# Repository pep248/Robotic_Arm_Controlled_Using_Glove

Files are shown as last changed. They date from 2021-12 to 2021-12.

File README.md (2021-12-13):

# Robotic arm controlled using an electronic glove

This repository contains a project with the mechanical design of a robotic arm meant to copy the movements of a user.
The arm has been mechanically designed using SolidWorks, and has been programed using Arduino.

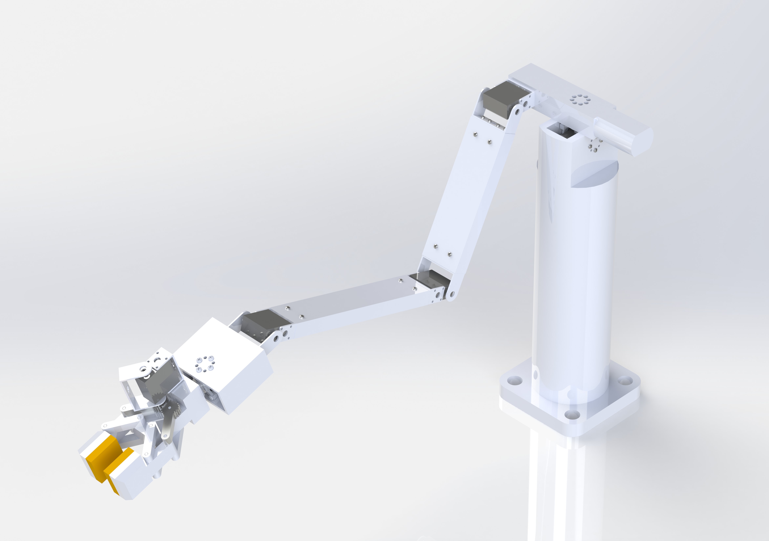
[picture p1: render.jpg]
Render


## Folders
* Inside the [Arduino](Arduino) folder, we can find the code and the libraries used to control the robotic arm using the glove.
* Inside the [MATLAB](MATLAB) folder, we can find the code used to simulate the robot motion. The folder includes the [Robotics Toolbox](https://petercorke.com/toolboxes/robotics-toolbox/) package from [Peter Corke](https://github.com/petercorke).
* Inside the [SolidWorks](SolidWorks) folder, we can find all the 3D parts and the assembly regarding the mechanical design of the robot.

## Author
* Josep Rueda Collell: rueda_999@hotmail.com

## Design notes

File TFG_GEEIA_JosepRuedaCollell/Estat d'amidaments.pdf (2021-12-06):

# Treball final de grau

## Estudi: Grau en Enginyeria Electrònica Industrial i

. | Automàtica

### Títol:

# Disseny d’un braç robòtic controlat per un guant electrònic

### Document 4: Estat d’amidaments

### Alumne: Josep Rueda Collell

### Tutor: Miquel Rustullet Reñe Departament: Enginyeria Elèctrica, Electrònica i Automàtica Àrea: Enginyeria de Sistemes i Automàtica

### Convocatòria: Juny/2019

Disseny d’un braç robòtic controlat per guant electrònic | Estat d’Amidaments

ÍNDEX:

### 1. Implementació electrònica del braç i mà

Descripció | Quantitat
Robot Digital Servo RDS5160 | 1
Robot Digital Servo RDS3135 | 1
Robot Digital Servo RDS3218 | 2
Digital Servo HS-785HB | 2
Cable DuPont Mascle-Mascle | 40
Cable DuPont Mascle-Femella | 80
DC-DC XH-M401 | 3
h Connectar i soldar els diferents components | 2
h Enginyer | 2
h Oficial de primera | 2

### 2. Implementació electrònica del guant i processador

Descripció | Quantitat
Arduino Uno | 1
MPU-6050 | 4
Multiplexor I2C TCA9548A | 1
Cable DuPont Mascle-Mascle | 40
Cable DuPont Mascle-Femella | 80
DC-DC XH-M401 | 1
Font GHB 12V | 1
Polsador B3F | 1
Placa fibra doble cara 80x120 mm | 1
Nucli de ferrita Vk200 | 1
Caixa elèctrica 746-903 Altech 450 mm x 300 mm x 94 mm | 1
h Connectar i soldar dels diferents components | 2
h Enginyer | 2
h Oficial de primera | 2

### 3. Implementació programa

Descripció | Quantitat
h Enginyer | 20

### 4. Posada en funcionament

Posta en marxa
Descripció | Quantitat
h Enginyer | 4
h Oficial de primera | 4

Josep Rueda Collell

Graduat en enginyeria Electrònica Industrial i Automàtica.

Girona, 6 de juny de 2019

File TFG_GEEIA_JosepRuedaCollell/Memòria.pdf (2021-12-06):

# Treball final de grau

Estudi: Grau en Enginyeria Electrònica | Industrial i
. | Automàtica

## Títol:

# Disseny d’un braç robòtic controlat per un guant electrònic

## Document 1: Memòria i Annexos

## Alumne: Josep Rueda Collell

## Tutor: Miquel Rustullet Reñe Departament: Enginyeria Elèctrica, Electrònica i Automàtica Àrea: Enginyeria de Sistemes i Automàtica

## Convocatòria: Juny/2019

Disseny d’un braç robòtic controlat per un guant electrònic | Memòria i annexos

INDEX:

Fig. 1: Logotip del Duve Institute

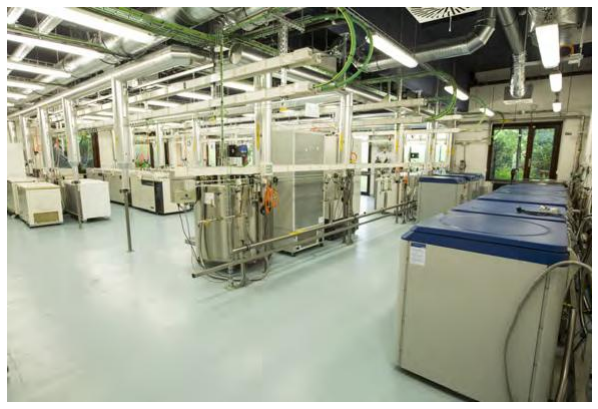
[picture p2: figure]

Fig. 2: Sala de preservació criogènica.

### 1. Introducció:

### 1.1 Antecedents

L’institut de Duve és un institut a Bèlgica enfocat a la recerca genètica i biotecnològica, el

qual disposa de varis laboratoris dins del campus de la UCL (Universitat Catòlica de

Louvain).

Aquest institut deu el seu renom a la política de centrar-se en la recerca amb finalitats

mèdiques, així com incentivar la política de col·laborar amb altres empreses del mateix

àmbit.

Per a la realització de les conseqüents investigacions, els seus laboratoris, estan equipats

amb estacions d’anàlisi, sales blanques, cambres hiperbàriques, sales de preservació

criogènica, estacions d’aïllament de proteïnes, entre d’altres instal·lacions.

El Sr. Marcel McCullough, científic dels laboratoris SCBD (Stem Cells Biology and

Development) del Duve Institute ens explica que, habitualment, en aquest àmbit de recerca,

s’han de fer processos en condicions potencialment perilloses, ja sigui perquè treballen amb

elements a temperatures massa fredes per ser aptes pel contacte humà o amb substàncies tòxiques o corrosives. Dur la conseqüent vestidura protectora, pot dificultar i, fins i tot,

impossibilitar la realització de certes tasques.

### 1.2 Objecte del projecte

L’objecte del projecte és dissenyar un braç robòtic, capaç de copiar els moviments d’un

guant, que duria un operari al voltant del braç juntament amb el programa que el controli.

### 1.3 Requeriments i abast

El braç ha de cabre dins una campana de laboratori de 1400 mm d’ample, 1100 mm d’alt i

800 mm de profunditat l’eix de la mà sempre ha d’anar paral·lel al terra, cap articulació

tindrà una velocitat superior a 0,4 rad/s i cap articulació tindrà una acceleració superior a 0,2 rad/s²

La feina del projectista acaba un cop dissenyada la solució del projecte i s’entrega el

projecte al client.

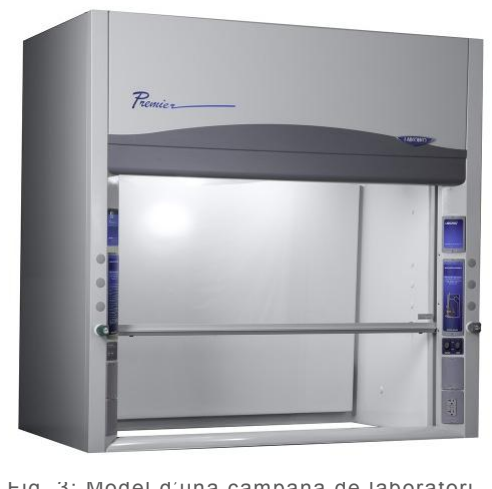
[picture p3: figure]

Fig. 3: Model d’una campana de laboratori

### 2. Conjunt braç

La idea proposada és construir un braç robòtic amb una estructura similar a la d’un braç

humà, capaç de moure i decantar provetes o altres recipients de caràcter similar. El braç ha

de ser capaç d’agafar i deixar una proveta o tub d’assaig, traslladar-lo en qualsevol dels 3

eixos.

Per fer aquestes combinacions concretes de moviments, hem escollit un disseny el qual és

incapaç de fer tots els moviments que podria fer un braç humà ja que implementar un braç

que els pogués fer, tenint en compte com de reduïdes són les tasques que se’ns exigeixen,

resulta redundant.

### 2.1 Estudi de forma

Tenint en compte que el braç haurà de treballar dins una campana d’un laboratori químic,

hem realitzat un estudi per veure quina és la forma més optima per fer-lo servir. Per a fer

aquest estudi, hem utilitzat les dimensions per a la campana descrites als requeriments del

projecte.

Desprès de provar amb varies longituds pels diferents components que conformen el braç i

varies localitzacions d’aquest dins la campana, hem acabat determinant dos possibles

casos, col·locar el braç perpendicular al vidre de la campana o col·locar el braç paral·lel al

vidre de la campana.

En el cas on tenim el braç perpendicular al vidre de la campana, estaríem obligats a fer el

tronc o esquena més llarg, a fi de poder aprofitar millor l’espai a dins de la campana.

La figura 4 ens presenta una vista lateral de la campana amb varies posicions dels tres

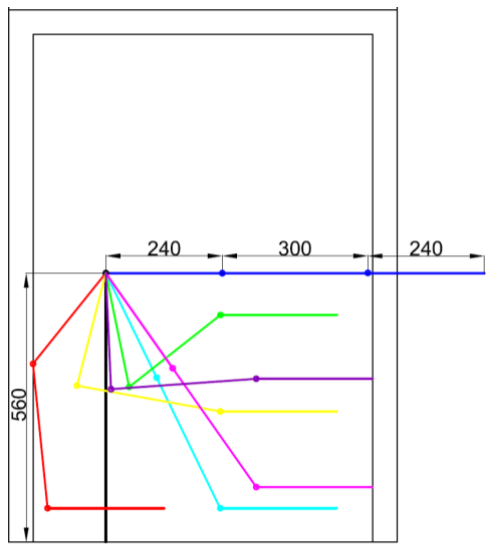
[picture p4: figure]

components del braç: braç avantbraç i mà, també en vista lateral.

Tal i com podem veure, amb aquesta distribució, podem controlar gran part de la base de la

campana, però no podríem estirar el braç completament, ja que xocaríem amb l’interior

d’aquesta.

Tanmateix, com que el robot copiarà els moviments que faci l’operari, aquesta distribució

pot resultar en moviments incòmodes o fins i tot impossibles de realitzar per a un ésser

humà, com per exemple, l’esquema representat amb color vermell on el canell hauria de

quedar pràcticament perpendicular al braç. En el cas de la distribució on tenim el braç

paral·lel al vidre de la campana, el tronc o esquena podria ser més curt, el qual ens

permetria més llibertat de moviment.

La figura 5 ens presenta una vista frontal de la campana amb varies posicions dels tres

components del braç en vista lateral. Tal i com podem veure a la figura, amb aquesta

distribució, podríem controlar molt més bé la profunditat de la campana a cost de menys

llibertat per controlar la base.

Fig. 4: Vista lateral de varies posicions del braç

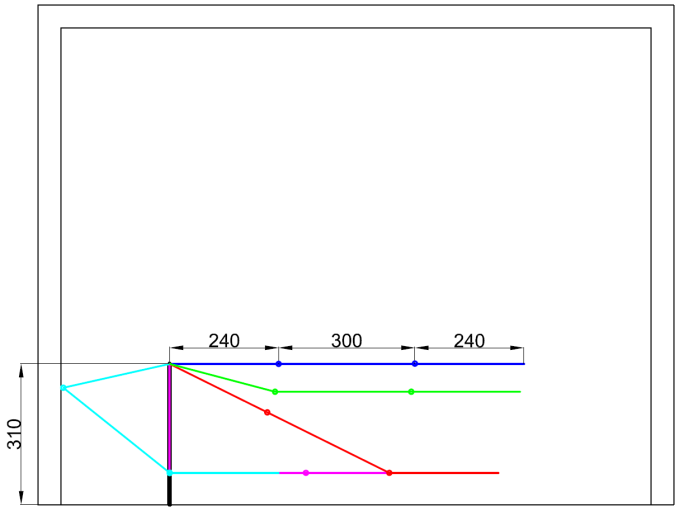
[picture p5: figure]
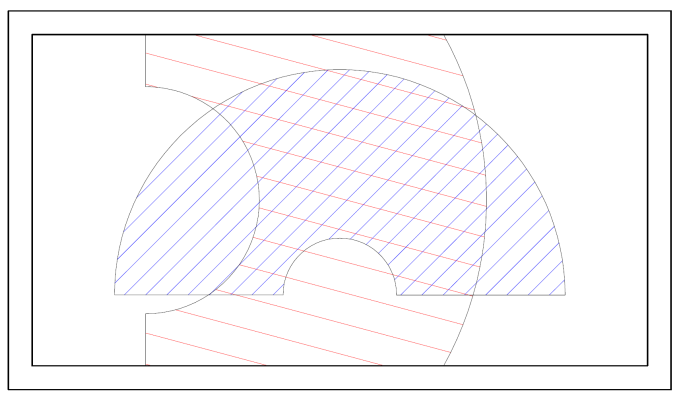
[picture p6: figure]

Fig. 6: Vista superior comparativa entre rangs

Fig. 5: Vista frontal de varies posicions del braç

Aquesta distribució no permet que l’operari baixi massa el braç ja que podria xocar amb el

terra amb molta més facilitat que al primer cas, per tant, és recomanable alhora que pràctic,

que l’operari s’assegui prop d’una taula la qual limiti els moviments del braç per sota

d’aquesta.

En definitiva, tal i com podem veure a la figura 6 ens presenta els rangs dels braços a nivell

del terra de la campana on el blau representaria el cas del braç perpendicular al vidre de la

campana i el vermell representaria el cas del braç paral·lel a aquesta.

El problema que ens presenta el cas del braç paral·lel al vidre és que tan si treballa arran de

terra com si treballa a certa alçada, quan gira corre el risc de xocar amb els límits de la

campana.

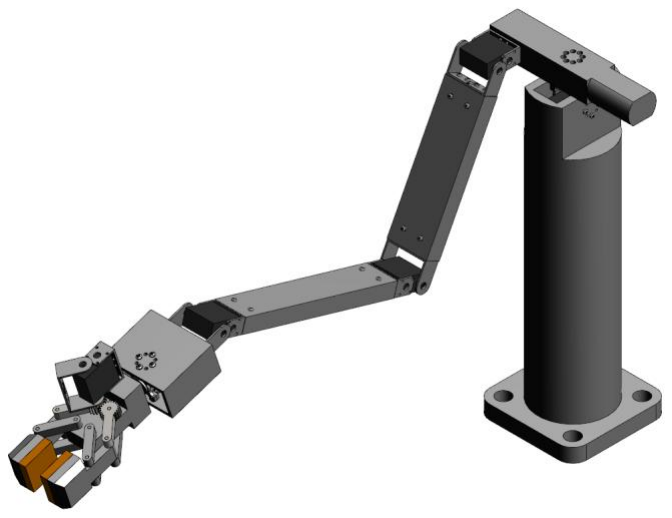
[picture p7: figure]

Fig. 7: Visualització de la solució proposada

Tanmateix, el rang del cas del braç paral·lel és superior al del cas del braç en perpendicular.

Tenint en compte el rang de treball superior del cas del braç paral·lel i la facilitat de control

del braç per part de l’operari, ens hem decantat per aquest cas.

La màquina es dissenyarà partint de la suposició que l’operari, per tal de controlar el braç,

es col·locarà, de costat, davant de la campana i girarà el cap per observar el moviment del

braç robòtic el qual copiarà, en paral·lel, els moviments del guant de l’operari.

### 2.2 Braç

Tenint en compte l’estudi de forma de l’apartat anterior, el braç no ha de poder fer tots els

moviments que podria acomplir un braç humà, dit això hem limitat el moviment del braç a

tan sols cinc graus de llibertat més l’accionament de la pinça.

Li hem donat una forma similar a la d’un braç humà, però hem optat per reduir la longitud

del braç i augmentar la de l’avantbraç, d’aquesta manera, els servomotors que

s’encarregaran de controlar les articulacions seran de valors més semblants.

L’estructura anirà muntada sobre la peça “base braç” la qual estarà cargolada al terra

mitjançant 4 cargols i faria la funció d’esquena, fent el paral·lelisme amb la fisiologia d’un

ésser humà.

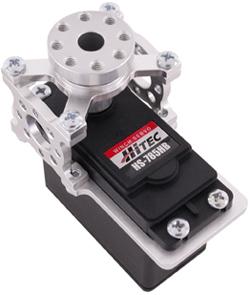
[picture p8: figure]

Fig. 8: Servo-block

Un servomotor el qual ens hi referirem com a “servomotor esquena” estarà col·locat a

l’extrem superior del la “base braç”. Aquest mitjançant l’ajuda d’un “servo-block” aguantarà

tota la resta de l’estructura.

El “servo-block” és una peça a mode d’esquelet per a servomotors que absorbeix el tallant i

el moment que altrament, es carregarien a l’eix d’un servomotor i que el podrien malmetre.

Una peça anomenada “espatlla” estarà col·locada sobre el “servo-block”. El “servomotor

esquena”, anteriorment esmentat, farà girar aquesta peça en un eix perpendicular al terra.

Aquesta peça degut a la seva complexa geometria l’haurem d’imprimir mitjançant una

impressora 3D i conseqüentment estarà composta de PLA per a impressora 3D

Aquesta peça “espatlla” en un costat hi tindrà el “servomotor espatlla” del qual hi penjarà la

resta del braç mentre que l’altre costat s’hi podrà col·locar un contrapès per contrarestar

part del moment que ha de suportar el “servo-block” si fos necessari.

Aquest “servomotor espatlla” tindrà connectat el braç, aquest estarà connectat, al

“servomotor colze”, aquest a l’avantbraç i aquest al “servomotor canell” del qual en penjaria

la pinça o mà.

Tots 3 servomotors (“servomotor espatlla”, “servomotor colze” i “servomotor canell”)

treballen sobre el mateix pla, el qual és perpendicular al terra i l’orientació del qual ve

determinada pel gir del “servomotor esquena”.

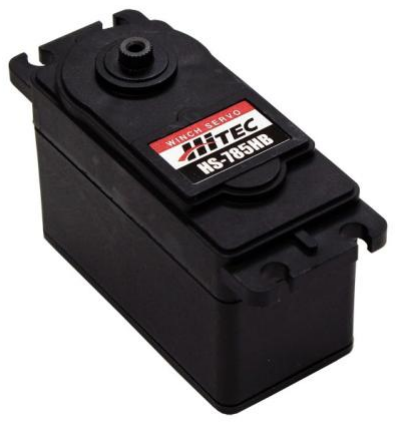
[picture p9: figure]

Fig. 9: Servo-motor HS-785HB

Voltatge: | 5 - 6 V
Parell: | 13,5 kg·cm (6 V)
| 31 kg·cm (6,8 V)
Pes | 60 g
Mida | 40 × 20 × 40,5

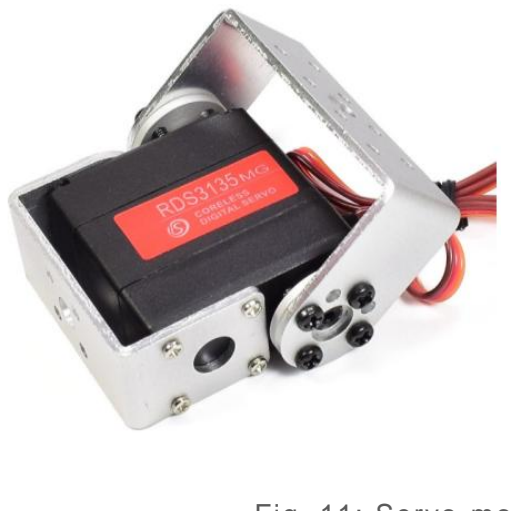
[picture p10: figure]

Fig. 10: Servo-motor RDS5160

Voltatge: | 6 - 8,4 V
Parell: | 58 kg·cm (6 V)
| 65 kg·cm (7,4 V)
Pes | 60 g 70 kg·cm (8,4 V)
Mida Pes | 64 × 55,6 × 20 162g
Mida | 65 × 30 × 48
Fig. 11: Servo-motor RDS3135 Voltatje: | 6 - 8,4 V
Parell: | 26 kg·cm (6 V)
| 31 kg·cm (7,4 V)
| 35 kg·cm (8,4 V)

A l’Annex A.2 Modelització matemàtica del braç, s’entra més en detall sobre el moviment del

braç.

2.2.1 Descripció dels components del braç

Hem calculat les necessitats mecàniques dels servomotors i conseqüentment hem escollit

els servomotors d’acord a aquestes necessitats.

Els servomotors, posteriorment descrits, no utilitzaran unitats del sistema internacional sinó

que expressaran el parell que poden subministrar en kg·cm ja que són les unitats que

s’utilitzen a nivell comercial.

Al “servomotor esquena” només se li oposaran les carregues inercials del braç. Degut al poc

pes dels components, la inèrcia és pràcticament negligible, conseqüentment hem agafat el

servomotor HS-785HB de la casa Hitec el qual està preparat per al nostre “servo-block”.

Aquest servomotor pot arribar a subministrar un parell de 13.2 kg·cm.

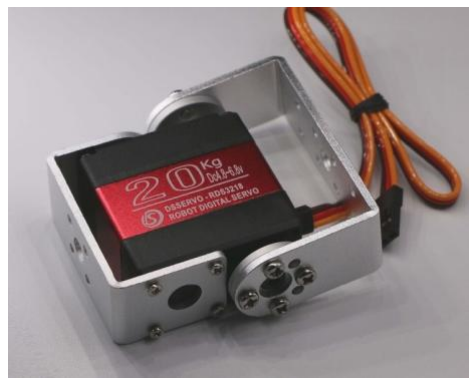
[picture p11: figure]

Fig. 12: Servo-motor RDS3218

Voltatge: | 5 - 6,8 V
Parell: | 20 kg·cm (5 V)
| 26 kg·cm (6,8 V)
Pes | 60 g
Mida | 40 × 20 × 40,5

El “servomotor espatlla”, tal i com indica el nom, estaria situat a l’espatlla i haurà d’aguantar

el pes i el moment de la resta de l’estructura del braç, per tant serà el servomotor de més

potència. Hem escollit el RDS5160 de la casa Robot Digital Servos, el qual pot subministrar

un parell de 60 kg·cm.

El “servomotor colze” estaria situat al colze. Hem escollit el RDS3135 de la casa Robot

Digital Servos, el qual pot subministrar un parell de 35 kg·cm.

El “servomotor canell” estaria situat al canell i és el que aguanta la pinça. Hem escollit

l’RDS3128 de la casa Robot Digital Servos, el qual pot subministrar un parell de 20 kg·cm.

El “servomotor espatlla”, “servomotor colze” i “servomotor canell” escollits prèviament,

venen equipats amb 2 orelles o “brackets” a fi de facilitar la unió entre 2 peces. Aquest

servomotors estan especialment dissenyats per a ser emprats com a articulacions per a

robots és per això que reben el sobrenom de “Robot Servo”. Hem escollit específicament

aquest tipus ja que faciliten molt tan el muntatge del braç com el control d’aquest.

La peça base braç tindrà allotjat dins seu un servo-block amb el conseqüent servomotor.

Aquest servo-block anirà collat a les parets de la peça base braç mitjançant cargols M3,5 x

8 mm. A l’extrem mòbil del servo-block hi col·locarem la peça espatlla i realitzarem la unió

mitjançant cargols M3,5 x 12 mm.

La peça espatlla anirà cargolada amb cargols auto-roscants a el “servomotor espatlla” i

aquest utilitzant també cargols auto-roscants estarà unit al component braç. Utilitzant

aquesta classe de cargols, no necessitem roscar forats a la peça ni tampoc necessitarem

allocar-hi forats per a les femelles.

El component braç estarà compost per un perfil rectangular d’alumini de 54,76 mm per

18,78 mm i 2,04 mm de gruix i tindrà una longitud de 228,4 mm.

Al seu interior hi tindrà allotjat a cada extrem un prisma de PLA. Aquest prisma anirà

cargolat al perfil d’alumini i a les orelles o “brackets” dels servomotors mitjançant cargols

auto-roscants.

El component avantbraç estarà compost per un perfil rectangular d’alumini de 45 mm per 20

mm i 1,2 mm de gruix i tindrà una longitud de 240 mm.

De la mateixa manera que amb el perfil rectangular del braç, utilitzarem prismes de PLA i

cargols auto-roscants per a fer la unió entre l’avantbraç i el “servomotor colze” i l’avantbraç i

el “servomotor canell”.

La peça espatlla i la peça base braç són peces de fabricació les quals degut a la seva

complexitat de mecanització es conformaran mitjançant tecnologies d’impressió 3D i

conseqüentment utilitzarem PLA com a material de fabricació.

Hem escollit perfils d’alumini buits ja que és un material molt lleuger alhora que resistent.

Cal recordar que hem escollit la mida dels perfils a fi de poder-hi allotjar a dintre un prisma

prou gros com per poder realitzar les unions amb les orelles o “brackets” dels servomotors.

Si no estiguéssim lligats a això, hauríem pogut escollir perfils molt més petits.

### 2.3 Descripció de la mà

La peça “base canell”, tal i com hem dit anteriorment, es connecta al “servomotor canell”.

Aquesta, allotjarà al “servomotor mà” el qual controlarà la rotació de la pinça sobre un eix

paral·lel respecte el terra, amb l’ajuda d’un “servo-block” que absorbirà les forces tallants i

moments que normalment descarregarien contra l’eix del servomotor

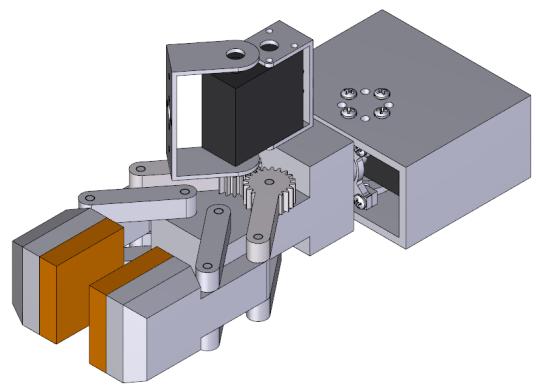
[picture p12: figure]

Fig. 13: Visualització 3D de la mà o pinça

Al extrem del “servo-block”, hi connectaríem la peça “base mà” sobre la qual hi construiríem

els mecanismes de la pròpia pinça.

Aquesta pinça, estarà constituïda per dos superfícies paral·leles recobertes de goma, que

actuarien a mode de pinça. Cada una d’aquestes superfícies paral·leles les quals

anomenarem “suport goma” està articulada per dos quadrats articulats que treballen en

paral·lel.

Una biela de cada quadrat articulat estarà dentada, a mode d’engranatge, a fi que totes

dues superfícies de la pinça puguin treballar de forma sincronitzada en simetria.

Un servomotor el qual anomenarem “servomotor pinça” i estarà col·locat sobre la mà i tindrà

una orella o “bracket” sobre la biela dentada i l’altre sobre la peça “base mà” i s’utilitzarà per

accionar el mecanisme de la pinça.

2.3.1 Descripció dels components de la mà

El “servomotor mà” estaria situat dins la peça “base canell” i és el que s’ocupa de la rotació

de la mà. De la mateixa manera que el “servomotor esquena”, aquest també va dins d’un

“servo-block”. Tenint en compte que l’únic parell a vèncer seria el vinculat al propi pes de la

proveta en decantar-la i les inèrcies del conjunt pinça i càrrega, optem per menysprear-ho,

per tant tornarem a escollir el servomotor específic per al “servo-block”, l’HS-785HB de la

casa Hitec, el qual pot subministrar un parell de 13.2 kg·cm.

El “servomotor pinça” estaria situat sobre la pinça i seria l’encarregat d’obrir-la i tancar-la.

Hem escollit l’RDS3135 de la casa Robot Digital Servos, el qual pot subministrar un parell

de fins a 20 kg·cm.

Totes les càrregues i pesos que estiguin aplicats a la pinça o a la mà són els més

desfavorables pel servomotor de l’espatlla, ja que al ser el punt més allunyat del servomotor,

el moment a suportar incrementa de forma dràstica per a masses relativament petites. Dit

això, per a realitzar el muntatge del mecanisme, enlloc d’utilitzar unions mecàniques

utilitzarem adhesiu.

Les varilles passaran a través de la peça “base mà” i aplicarem adhesiu a les bieles perquè

es mantingui subjecte.

El servomotor, tal i com havíem dit anteriorment, tindrà una orella o “bracket” a la “peça mà”

i una altra a una de les bieles dentades. Aquestes bieles dentades tindran un diàmetre

primitiu de 20 mm i un mòdul de 0,75 el qual equivaldria a 15 dents, si fos un engranatge

complert.

Hem escollit un nombre de dents imparell a fi que els 2 engranatges puguin encaixar entre

ells sense quedin desfasats mig pas. El centre instantani de rotació entre les dos bieles

dentades no és estàtic com seria el cas d’una xarnera, sinó que es desplaça segons la

posició de les bieles. Tenint en compte això, hem col·locat l’eix de rotació del servomotor

sobre l’eix de rotació d’un dels engranatges.

Per a unir el servomotor amb la pinça, també utilitzarem adhesiu, no només per la manca de

pes que això implica, sinó també perquè les orelles o “brackets” del servomotor no tenen

forats o encaixos amb els que realitzar unions amb peces mecàniques.

### 2.4 Guant

El guant estaria conformat per una tela que recobriria tot el braç on hi hauria adherits els

sensors. Els sensors estarà adherits amb unes abraçadores de tipus “velcro” que ajudaran a

ajudar i fixar el guant i els sensors al lloc adient sobre el braç humà.

Els sensors estaran adherits mitjançant adhesiu a sobre les abraçadores per tal de poder-

les orientar correctament abans de ser utilitzades. Aquests sensors, seran quatre giroscopis, els quals estaran repartits pel braç, esquena i mà, i un polsador a la punta del polze per a

accionar la pinça.

2.4.1 Descripció dels components del guant

Hem escollit com a giroscopis els giroscopis MPU-6050, els quals poden llegir velocitats i acceleracions tan lineals com angulars en tots tres eixos, i envien les dades per canal I²C al

processador, en aquest cas, un Arduino Uno.

El protocol I²C te una velocitat per enviar i rebre dades de100 kbits per segon mitjançant un

bus sèrie el qual permet penjar-hi tants dispositius com necessitem. Tenint en compte que

haurem d’adquirir dades des de 4 sensors diferents, de forma simultània i de forma continuada, haver escollit un sensor amb protocol I²C resulta una elecció excel·lent.

El primer giroscopi anirà darrere l’espatlla i controlarà l’angle de gir de l’esquena respecte el

terra, és a dir, l’angle del pla on treballaria la resta del braç. Un segon, situat a prop del

colze controlarà la rotació del que pròpiament dit, seria el braç respecte l’espatlla. Un tercer

a l’avantbraç, com més allunyat del colze millor per tal de captar amb més precisió la rotació

de l’avantbraç respecte el colze.

S’ha de tenir en compte, que si el situem sobre una part del braç que roti sobre un eix

diferent que el del colze ens podria alterar les lectures del giroscopi, s’ha d’intentar que els

giroscopis romanguin perpendiculars al eix de treball.

El quart giroscopi estarà col·locat al revers de la mà i controlarà la rotació de la pinça.

És de suma importància que els sensors tinguin l’eix de treball perpendicular o paral·lel al

pla del terra, tal i com s’indica a la figura 14. Com més alineats treballin al seu eix teòric de

funcionament, més fidels seran les lectures del sensors.

Tal i com s’ha especificat anteriorment, no ens caldrà un giroscopi per a calcular la

orientació del canell. El canell sempre s’encarregarà que la mà o pinça estigui paral·lela al

terra, i podem calcular la inclinació d’aquest a partir de les lectures del braç i l’avantbraç.

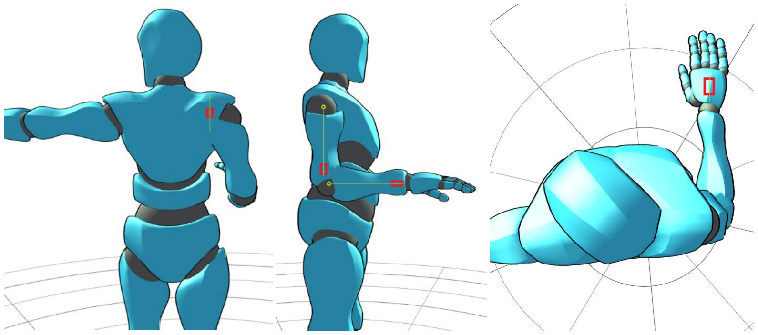
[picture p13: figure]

Fig. 14: Vista anterior, lateral i superior, amb la localització dels giroscopis

Tal i com s’explica més endavant, en l’apartat 2.5 Hardware, aquests giroscopis duen una

adreça interna que desencadena problemes d’identitat quan se’n connecta més d’un alhora a un Arduino, per tant, ens veiem obligats a utilitzar un multiplexor I²C.

El polsador, el qual estarà col·locat sobre el polze i que podrem accionar prement-lo contra

l’índex serà de característiques binaries (obrir o tancar), per tant, no permetrà un control

analògic de la obertura de la mà, és a dir, que sempre farà la mateixa força contra qualsevol

proveta.

Fig. 15: Arduino Uno

Operating Voltage | 5V
Input Voltage (recommended) | 7-12V
Input Voltage (limit) | 6-20V
Digital I/O Pins | 14 (of which 6 provide PWM)
PWM Digital I/O Pins | 6
Analog Input Pins | 6
DC Current per I/O Pin | 20 mA
DC Current for 3.3V Pin | 50 mA
Clock Speed | 16 MHz
Length | 68.6 mm
Width | 53.4 mm
Weight | 25 g

### 2.5 Hardware

Com a processador central, hem utilitzat una placa de tipus “Arduino Uno”. Aquesta placa és

cada cop més utilitzada per a aplicacions de caràcter professional degut a la facilitat d’us i a

l’ample ventall de sensors, actuadors i software així com altres dispositius, que permeten

compatibilitat amb ell. Tanmateix, també duu incorporat sistemes de protecció contra

sobretensions i curtcircuits, el qual el fan un dispositiu molt robust i segur.

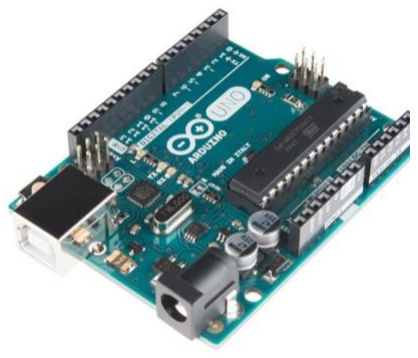
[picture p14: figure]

Tal i com hem explicat anteriorment, com a giroscopis utilitzarem el sensors MPU6050. El

rang de velocitat d’aquests giroscopis és molt superior a la velocitat de moviment d’un braç

humà. Referent a la sensibilitat aquesta és molt superior a la que se’ns exigia com a

condició de funcionament, per tant és adequat.

Tanmateix, el contractista vol tenir llibertat per a realitzar canvis i millores al disseny original

al llarg del temps, si ho troba necessari, per tant reafirmem la tria d’aquest dispositiu com a

processador central.

També cal afegir, que tal i com s’explica més endavant, en l’apartat 3.2 Llibreries, aquests

giroscopis poden corregir l’error d’integració de la posició utilitzant els eixos de la gravetat

per a orientar-se, per tant, podem afirmar que aquest component és ideal per al nostre

projecte.

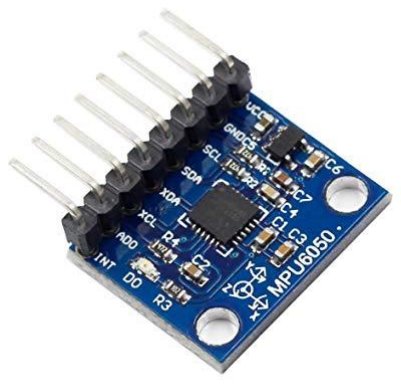
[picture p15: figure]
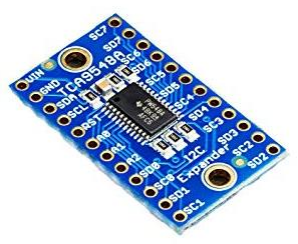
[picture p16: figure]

Fig. 17: TCA9548A

VCC | 1,65 V - 5,5 V

Cada un dels sensors, es comunica amb la unitat de control mitjançant protocol I²C. Cada

sensor te assignada internament la adreça 0x68 i disposa d’un pin digital per poder-la

canviar a 0x69. Si hi ha un conflicte d’adreces entre dos o més sensors, la unitat de control

es bloqueja i obliga a fer un reinici forçat a base de treure-li l’alimentació i tornar-li a posar.

Originalment es recomanava assignar a tots els sensors l’adreça 0x69 tret del que volíem

llegir, que li assignaríem la adreça 0x68 mitjançant una de les sortides digitals del

controlador, val a dir, que tal i com hem dit abans, tot i que no estiguem llegint en cap

moment de l’adreça 0x69, com que hi ha un conflicte d’adreces per part dels altres tres

sensors de forma simultània, multiplexar els sensors utilitzant les sortides digitals del

controlador, resulta ser una opció inviable.

Fig. 16: MPU6050

VCC | 2.38 V - 5.46V

Giroscopi

Rang | ± 2000 º/s
Sensibilitat | 0,2 º/s

Acceleròmetre

Rang | ± 16 g
Sensibilitat Eix X | ± 0,05 g
Sensibilitat Eix Y | ± 0,05 g
Sensibilitat Eix Z | ± 0,08 g

Dit això ens veiem obligats a utilitzar un multiplexor I²C, en aquest cas, el Multiplexor

TCA9548A .

El multiplexor TCA9548A te tres entrades digitals que li permeten modificar la seva adreça

interna de 0x70 fins a 0x77. Això es fa servir per quan utilitzem varis multiplexors alhora, fins

a un màxim de 8 multiplexors per a un total de 64 sensors.

Tanmateix aquest multiplexor te un registre intern que des de la unitat de control, utilitzant

una comanda, podem controlar quin dels 8 ports interns volem escollir.

Dit això, tot i que tots els sensors tenen la adreça interna de 0x68, ja no hi ha conflicte

d’adreces ja que és el multiplexor qui va alternant entre els diferents dispositius però la

nostra unitat de control només veu la seva adreça, la qual és 0x70.

Finalment, tal i com podem veure als plànols hem col·locat un llit de ferrita entre les masses

de la part digital i la part analògica. En ocasions podem observar com la part digital d’uns

sistema causa interferències a la part digital analògica. Per evitar-ho utilitzem un llit de

ferrita, el qual actua com una inductància, és a dir, un filtre pas baix per a soroll d’alta

freqüència. D’aquesta manera donem més robustesa al sistema.

### 2.6 Consum

En aquest apartat estudiarem les necessitats energètiques dels diferents components

elèctrics i electrònics alhora d’escollir una font.

La intensitat consumida pels sensors i el multiplexor són de l’ordre de μA. Tenint en compte

que són tan baixos, els menysprearem.

L’Arduino, consumeix 0,05 A per sortida. Si ha de controlar 6 motors i el polsador, podem

arrodonir a 0,4 A.

D’acord amb el document plànols, podem veure que els servomotors estan agrupats en

grups de dos i cada parella de servomotors estan alimentats pel mateix convertidor. Això és

degut a que per suplir les demandes de parell dels diferents servomotors, tal i com veiem a

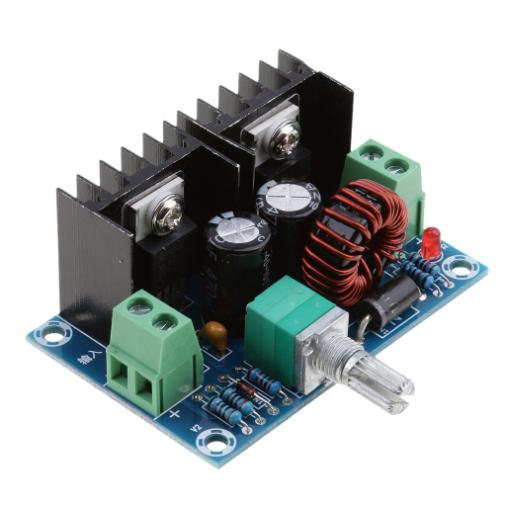
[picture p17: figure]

Fig. 18: XH-M401

Regulating mode: | PWM
Input voltage: | DC 4 - 40V
Output range: | DC 1.25 - 36V
Maximum current: | 8A
Maximum power: | 200 W
Conversion efficiency: | 94%
Switching frequency: | 180KHz
Size: | 61 × 41 × 27mm

(Eq. 1)

les conseqüents “datasheet’s”, necessitem un voltatge específic, i en el cas de varis

servomotors, aquest coincideix.

Les pèrdues dels convertidors es quantificaran, tenint en compte el rendiment. Cal recordar

que l’Arduino, també estarà alimentat per un convertidor però a diferència dels altres

dispositius, aquest no ha de compartir el convertidor.

Haurem de tenir en compte que aquests convertidors seran regulables, dit això, quan

s’implementi, l’operari, amb l’ajuda d’un multímetre, s’haurà d’assegurar que regula el

potenciòmetre de cada convertidor de forma correcte per a tenir el voltatge adequat a la

sortida, tal i com s’indica als plànols.

Primerament, comprovarem que els convertidors, poden suplir les nostres necessitat

d’intensitat i de potència.

El convertidor que haurà de suportar més potència, serà el que ha d’alimentar els

servomotors del colze i de l’espatlla quan aquests han de suportar el parell màxim ja que

son els motors de major potència. Tanmateix el consum dels servomotors no es pot trobar a

la seva “datasheet”, conseqüentment, de forma experimental, hem mesurat el corrent de

cada un dels servomotors pel cas més desfavorable, és a dir, quan el parell a resistir sigui

màxim.

(Eq. 3)

(Eq. 2)

El “servomotor espatlla” pel qual hem escollit el RDS5160, i el “servomotor colze” pel qual

hem escollit el RDS3135 els quals s’alimenten a 8,4 V, tenen un consum aproximat de 3 A i

1,2 A respectivament. Si utilitzem la formula de la equació 1, això es tradueix a 35,3 W de

potència i 4,2 A, molt per sota de les limitacions de potència del convertidor.

Seguidament calcularem les necessitats energètiques dels altres convertidors, a fi de poder

calcular el consum total:

El “servomotor canell” i el “servomotor pinça” pels quals hem escollit el RDS3218 i els quals

s’alimenten a 6.8 V, tenen un consum aproximat de 0,8 A cadascun. Això es tradueix a 10,9

W de potència i 1,6 A.

El “servomotor esquena” i el “servomotor mà” pels quals hem escollit el HS-785HB i els

quals s’alimenten a 6 V, tenen un consum aproximat de 0,4 A cadascun. Això es tradueix a

4.8 W de potència i 0,8 A.

Utilitzant la següent fórmula, podem calcular la potència que ha de subministrar la font:

Hem de tenir en compte que hem menyspreat els sensors. També hem de recordar que el

rendiment dels convertidors, acordant amb la “datasheet” és de 0,94.

La potència consumida pel sistema seria, doncs, de 56,4 W.

Ens hem decantat per la font GHB 12V, la qual pot suplir les nostres necessitats

energètiques i duu refrigeració incorporada. A més els pins van agrupat en parelles, la qual

cosa implica que tenim el doble de pins de Vout i de GND, la qual cosa facilitaria la

instalació tenint en compte que hem de conectar 4 convertidors al darrere.

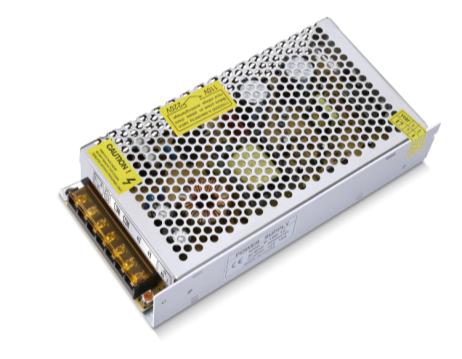
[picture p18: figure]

Aquests 56.4 W per a una sortida de 12 V es traduirien a 4.7 A, els quals estan per sota de

les limitacions de la font.

Fig. 19: GHB 12V

Vin | 230 V ~
Vout | 12 V ⎓
Imax | 15 A
Pmax | 180 W

### 3. Descripció del programa

### 3.1 Funcionament del programa

Inicialment hem parametritzat les condicions inicials com serien les longituds dels eixos del

braç i les dimensions en l’eix X de la campana. Seguidament els hi assignem una variable

constant.

El processador, adquireix la lectura dels angles de cada sensor de forma continuada.

Cada cop que s’executa el programa, pren aquests valors dels angles prèviament adquirits, i

en calcula la posició X, Y i Z mitjançant cinemàtica directe. El programa activa un pilot per

assegurar-se que aquesta operació només es realitzi un cop cada 4 segons, tot i que els

sensors no deixen en cap moment d’adquirir els valors dels angles.

Seguidament, el programa comprova si aquesta posició X de la pinça és dins de la dimensió

X de la campana. Si és a dins, transmet els valor dels angles al seus respectius

servomotors. Si fos fora, i transmetéssim els angles als servomotors implicaria que la pinça

xocaria amb les parets de la campana, per tant, si es a fora, assignem al valor X de la

posició de la pinça, el mateix valor X del límit de la campana i li fem calcular un altre cop,

mitjançant cinemàtica inversa, els valors del angles de cada articulació. Finalment assignem

els nous angles calculats al seu respectiu servomotor.

Cal recordar que el “servomotor canell” no te assignat cap giroscopi. L’angle de gir que se li

envia a aquest servomotor, es calcula en funció dels angles de l’espatlla i del colze a fi de

sempre estar paral·lels al pla del terra.

La rotació de la mà, portada a terme pel “servomotor mà”, no està subjectada a cap dels

càlculs anteriors. Tal i com podem veure al ANEX A.2 Modelització matemàtica del braç, per

poder simplificar els càlculs matricials, no hem tingut en compte la rotació de la mà en les

equacions, ja que només repercuteix en la rotació del punt final del braç, no en la posició en

cap els 3 eixos d’aquesta.

Finalment, desprès d’haver enviat les consignes d’angle als servomotors, es comprova si el

polsador ha estat premut o no a fi de controlar la obertura i el tancament de la pinça

utilitzant el “servomotor pinça”.

Un cop han passat 4 segons, es fa un “reset” del pilot que s’ocupava que els càlculs només

es realitzessin un cop per cicle, i es fa un “reset” al “timer” a fi de tornar a iniciar un cicle.

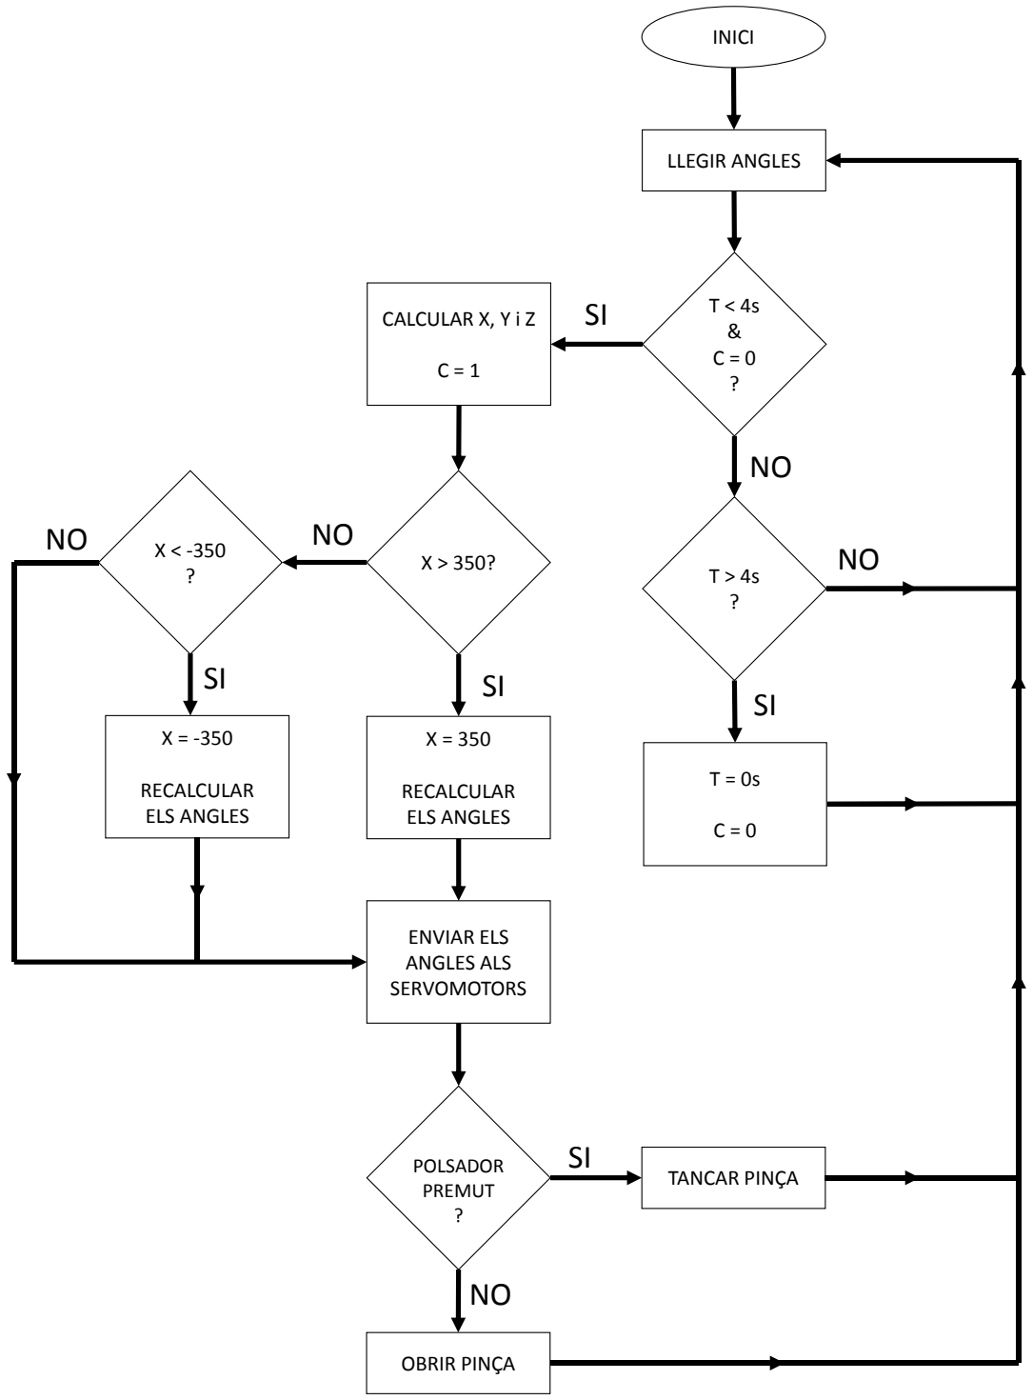
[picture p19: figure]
LLEGIR ANGLES; CALCULAR X, Y i Z; RECALCULAR ELS ANGLES; ENVIAR ELS ANGLES ALS SERVOMOTORS; INICI; TANCAR PINÇA POLSADOR PREMUT ?; OBRIR PINÇA

Fig. 20: Diagrama de flux del programa

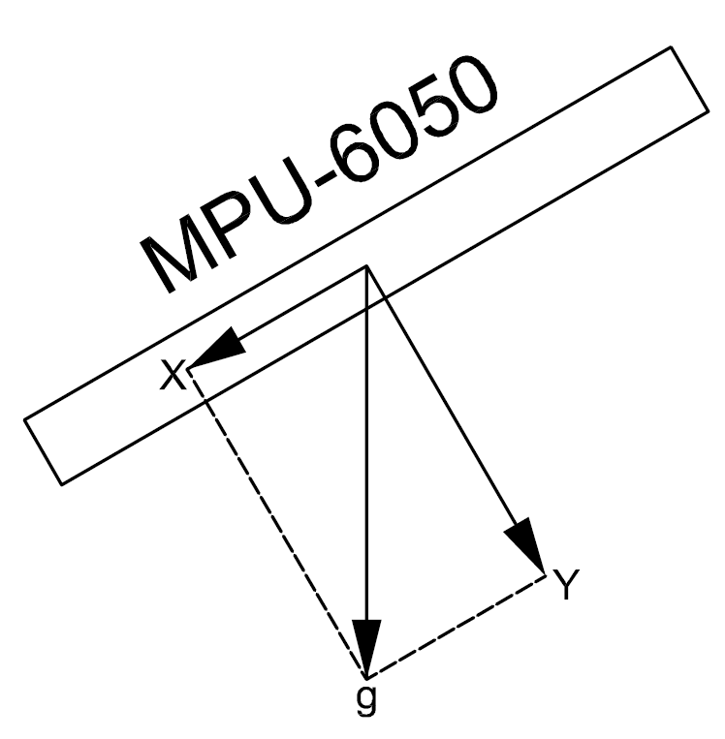
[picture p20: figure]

Fig. 21:Lectura de la força de la gravetat en dos eixos en un giroscopi

### 3.2 Llibreries

Hem utilitzat una llibreria especifica anomenada “MPU6050_tockn” la qual serveix per a

adquirir totes les dades possibles que ens pot donar el giroscopi “MPU6050” les quals

inclouen acceleracions, acceleracions angulars, velocitats i velocitats angulars en tots 3

eixos i que incorpora un integrador per a calcular el desplaçament i el gir.

Cada llibreria te assignades les adreces internes necessàries per a connectar-se amb el

giroscopi així com tot un seguit de subrutines que l’usuari pot utilitzar per a adquirir els

valors de les lectures desitjades.

A més la llibreria duu incorporada un tros de codi que utilitza la gravetat per a poder corregir

l’error d’integració del gir.

Cada sensor, s’ha estudiat en quin eix treballarà. Partint d’aquí, s’ha retocat el codi perquè

en funció de les lectures de la gravetat dels altres dos eixos, pugui calcular la seva inclinació

i corregir el valor instantani del gir.

El sensor que controla el gir de l’esquena, el qual gira en un pla perpendicular al terra, i

conseqüentment, paral·lel a la gravetat, no pot corregir aquest error, per tant, duu incorporat

un filtre de soroll, que menysprea les lectures de velocitat dins el rang de ± 0.5 º/s, per tal

que no s’acumuli error, almenys, mentre el sensor romangui quiet.

Tenint en compte els aspectes anteriors, cada sensor, disposa de la seva pròpia llibreria

amb les particulars modificacions que repercuteixen al seu concret funcionament.

Per defecte, el compilador d’Arduino, inclou la llibreria “servo.h” la qual ofereix un sistema

fàcil d’utilitzar per a controlar servomotors. Tanmateix nosaltres hem optat per a utilitzar la

llibreria “VarSpeedServo.h” la qual ofereix les mateixes prestacions que l’anterior en quant a

control de posició, amb la possibilitat de controlar la velocitat de gir escollint valors des de 1

a 255 on 1 és molt a poc a poc i 255 a màxima velocitat.

Seguidament prosseguirem a les funcions utilitzades en el programa principal que provenen

de les llibreries:

mpu6050X.update();

Aquesta funció ordena als sensors que refresquin els seus valors actuals.

mpu6050X.calcGyroOffsets();

En iniciar el programa, aquesta comanda fa que el giroscopi X, on X representa el sensor

segons el criteri anteriorment imposat, calibri els seus offsets interns per tal d’eliminar o

reduir els errors de lectura. Aquesta funció s’executa un cop per a cada sensor i aquests

han de romandre quiets durant el procés.

mpu6050X.getAngleX();

EL programa obté el valor del gir en l’eix X. Val a dir que hem modificat totes les llibreries

perquè l’eix X s’adapti al eix de gir en el que treballarà el guant, prèviament descrit al apartat

2.4 Guant.

### 3.3 Funcions

El programa està organitzat sobre un simple bucle o “loop” el qual crida les conseqüents

funcions quan les necessita. En aquest apartat les explicarem.

Hi ha funcions que van lligades a llibreries especifiques per a cada sensor, tal i com havíem

explicat a l’apartat anterior, dit això, quan es parli del sensor 0 estarem parlant del sensor

que detecta la rotació de l’esquena, quan es parli del sensor 1 estarem parlant del sensor que llegeix la inclinació de l’espatlla, quan es parli del sensor 2 estarem parlant del sensor

que llegeix la inclinació del avantbraç i, finalment, quan es parli del sensor 3 estarem parlant

del sensor que identifica la rotació de la mà.

Començarem per les funcions declarades al propi codi principal:

void tcaselect(X);

Utilitzant aquesta funció podem escollir amb quin dels sensors ens comunicarem, on X

representa el sensor segons el criteri anteriorment imposat.

void adquirir_dades();

Aquesta funció adquireix els valors dels angles de tots els sensors.

void motors();

Aquesta funció transmet els valors corresponents dels angles als conseqüents servomotors.

void imprimir_sensors();

Aquesta funció també s’usa exclusivament amb finalitats de “debbuging”. Ens imprimeix els

valors “raw” llegits directament dels sensors, sense que hagin estat tractats de cap manera.

void calculs();

Aquesta funció calcula el valor de la posició de la pinça utilitzant cinemàtica directa,

comprova si la X surt fora de la campana, tal i com hem explicat a l’apartat anterior, i si és

necessari, recalcula els angles que ho requereixin.

void imprimir_valors();

Aquesta funció també s’usa exclusivament amb finalitats de “debbuging”. Ens imprimeix els

valors dels angles, i de la posició de la pinça, així com els angles recalculats en el cas que

ho hagin hagut de ser.

### 4. Resum del pressupost

El pressupost d’execució té un cost de dos mil dos-cents tretze euros i quaranta cèntims,

sense IVA.

### 5. Conclusions

Aquest braç està pensat per treballar dins d’una campana de químics, a fi de realitzar

tasques en unes condicions on un braç humà no podria fer-ho correctament degut al risc a

les lesions i perjudicis contra entitats humanes. Alhora s’ha de tenir en compte la dificultat

que implica per a una persona, treballar amb la càrrega dur un equip de protecció, el qual

sol minar les capacitats humanes a cost d’incrementar la seguretat per a certes tasques.

El resultat ha estat un braç de 5 graus de llibertat més el control de la obertura de la pinça.

Tanmateix, el requeriment que la mà de la pinça s’havia de mantenir sempre paral·lela al pla

del terra, fa que virtualment sigui un robot amb 4 graus de llibertat més el control de

l’obertura de la pinça.

El disseny del braç no permet que la pinça topi contra el vidre de les parets de la campana

on treballa, tal i com s’havia especificat als requeriments i ja que la normativa no permet.

Tanmateix si que podria topar contra el terra, ja que no s’ha tingut en compte cap limitació

respecte aquest.

Quan l’operari obliga al robot a fer un moviment, el qual faria xocar el braç contra el vidre de

la campana, el programa, tal i com s’havia especificat als requeriments s’ha d’abstenir de

topar-hi. Quan es dona aquesta situació, el braç passa per un seguit de càlculs amb base

trigonomètrica que li permeten emular moviments semblants als de l’operari en quant al

desplaçament lineal de la pinça, però divergents en quant als valors absoluts dels angles de

les articulacions del guant.

El braç te limitacions respecte als angles de treball. Les equacions amb base trigonomètrica

que el nostre sistema duu integrades, poden calcular varis valors diferents pels angles per a

certes posicions del braç. D’aquí que puguin sorgir interpretacions errònies de la posició real

del braç. Dit això, l’operari s’ha d’abstenir a que la espatlla, tingui una inclinació superior a

un pla paral·lel al terra. Recordem que aquesta limitació només sorgeix quan hi ha risc que

el braç topi amb les parets de la campana.

El braç te un temps de resposta de 4 segons o menys en funció del punt on es trobés del

“loop” en el programa. Es podria haver implementat el programa de tal manera que el

programa s’hagués anat executant de forma continua, enlloc de utilitzant cicles de 4 segons,

però tenint en compte que el braç ha de transportar substàncies perilloses, ens ha semblat que fer-ho per etapes facilitaria la feina al operari ja que aniria més a poc a poc i li

transmetria una sensació de seguretat.

Josep Rueda Collell

Graduat en enginyeria Electrònica Industrial i Automàtica.

Girona, 6 de juny de 2019

### 6. Relació de documents:

Aquest projecte conté els següents documents: Memòria, Plànols, Plec de Condicions, Estat

d’Amidaments i Pressupost.

### 7. Glossari

USB | Bus Sèrie Universal
PLA | Àcid Polilàctic

I

2C | Inter-Integrated Circuit

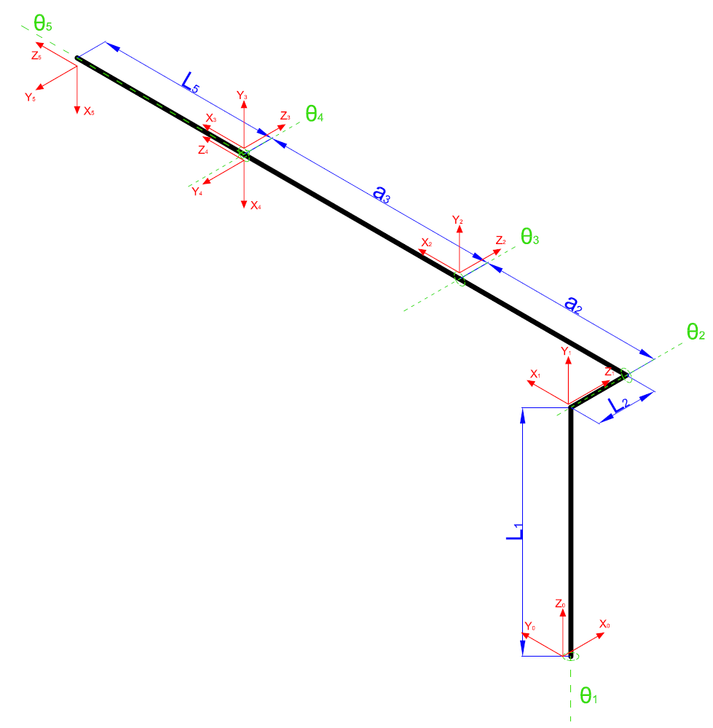
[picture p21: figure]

Fig. 22: Representació vectorial del braç robòtic des d’un punt de vista isomètric

A. CÀLCULS

A.1. Modelització matemàtica del braç

Tal i com s’ha explicat en l’apartat 3.1 funcionament del programa de forma continuada

haurem d’aplicar cinemàtica directe a fi de trobar la posició X, Y i Z de la punta del final del

braç en funció de θ1, θ2, θ3, θ4 i θ5, essent θ1 l’angle de rotació de l’esquena, θ2 l’angle de

rotació de l’espatlla, θ3 l’angle de rotació del colze, θ4 l’angle de rotació del canell i θ5 l’angle

de rotació de la pinça.

Tanmateix, també haurem de ser capaços de trobar els valors de θ1, θ2, θ3, θ4 aplicant

cinemàtica inversa quant li proporcionem X, Y i Z.

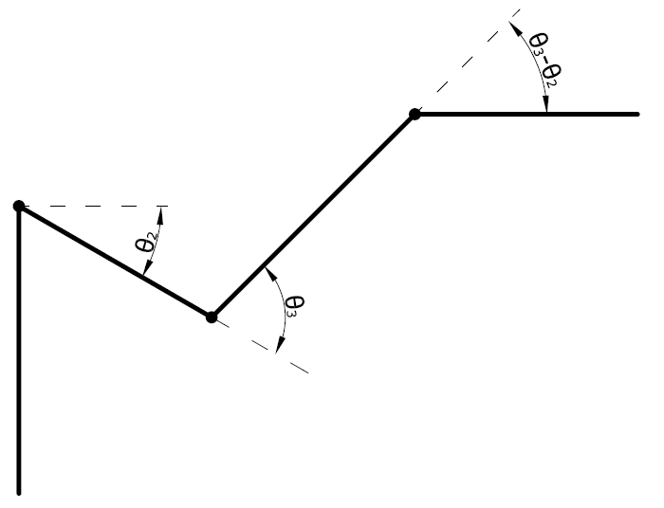
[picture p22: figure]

Fig. 23: Representació gràfica de la relació entre θ4 i θ2 i θ3.

Per tal de poder aplicar la cinemàtica directe i la cinemàtica inversa, anteriorment

esmentades, necessitem modelitzar tot el sistema a un model matemàtic.

Utilitzant matrius de rotació i matrius de translació podem transforma el sistema de la figura

a una matriu en funció de totes les variables.

A la figura anterior podem veure un braç modelitzat amb simples vectors en una perspectiva

isomètrica. Els eixos negres representarien cada eix físic del robot. De color blau hi ha

acotades les variables amb les quals reconeixem cada dimensió del braç.

De color verd, els eixos de rotació de les articulacions.

Finalment, de color vermell hi ha representats els eixos de coordenades amb els quals

podem parametritzar la orientació de cada eix.

Tal i com hem explicat anteriorment, només volem buscar les coordenades X, Y i Z de la

punta del braç. La orientació no ens és d’utilitat. Dit això, a l’hora de realitzar els càlculs no

tindrem en compte θ5 ja que només repercuteix l’angle de rotació de la pinça.

L’angle de rotació del canell, el qual està vinculat a θ4, no està enllaçat a cap sensor, tal i

com hem explicat anteriorment.

(Eq. 4)

θ

θ
θ

θ

(Eq. 5)

(Eq. 6)

(Eq. 7)

L’eix de treball de la pinça sempre ha de romandre paral·lel al pla del terra, per tant, tal i

com podem veure a la figura, podem eliminar una variable, si suposem la següent igualtat:

A.2. Càlcul matricial

La ultima columna de la matriu és la única que utilitzarem perquè és la única que fa

referencia a la posició.

Per obtenir la matriu del sistema, hem d’escriure en sèrie totes les matrius de rotació i

translació en ordre.

En acord amb la figura 29 anirem resseguint el moviment de cada origen de coordenades

(els eixos de color vermell) seguint les lleis de Denavit–Hartenberg.

Equacions del nus 0 al nus 1:

(Eq. 8)

(Eq. 9)

(Eq. 10)

(Eq. 11)

I en acord a les equacions anteriors obtenim la següent:

Equacions del nus 1 al nus 2:

I en acord a les equacions anteriors obtenim la següent:

Equacions del nus 2 al nus 3:

(Eq. 13)

(Eq. 12)

I en acord a les equacions anteriors obtenim la següent:

Equacions del nus 3 al nus 4:

I en acord a les equacions anteriors obtenim la següent:

Que segons la equació 4 ens queda:

(Eq. 18)

(Eq. 16)

(Eq. 17)

(Eq. 14)

(Eq. 15)

(Eq. 20)

Les equacions del nus 4 al nus 5, tal i com hem explicat anteriorment, les podem

menysprear.

I en acord a les equacions anteriors obtenim la següent:

De la matriu

només ens n’interessen les caselles X, Y i Z les quals resulten massa

extenses per a ser plasmades al projecte, però tal i com hem explicat a l’apartat 3.1

Funcionament del programa el processador ha de realitzar aquest càlcul periòdicament i de

forma continuada, per tant, la trobarem escrita dins els codi d’Arduino.

Seguidament, tal i com hem explicat a l’apartat 3 Descripció del programa, el programa,

mitjançant cinemàtica inversa ha de ser capaç de trobar els valors de θ1, θ2, θ3 quan li

proporcionem els valors de X, Y i Z.

Per a realitzar aquesta tasca, hem utilitzat un “solver” com seria el de Maple, li hem

introduït, les equacions de X, Y i Z obtingudes a l’apartat anterior i hem aïllat les equacions

de cinemàtica inversa de θ1, θ2, θ3 en funció de X, Y i Z.

Moltes d’aquestes equacions, tenen una base trigonomètrica, on ens podíem trobar que θ1,

θ2, θ3, tinguessin més d’un valor real.

(Eq. 19)

(Eq. 21)

Per evitar varis resultats per a les mateixes equacions, hem utilitzat el “solver” anteriorment

esmentat, per a dos casos diferents, quan el braç és a la dreta i quan el braç és a

l’esquerra.

Dit això, quan observem el codi, podrem trobar sis equacions. Tres d’aquestes per una

direcció i tres més per a l’altre.

Tot i això, hem hagut de retallar els angles fins a certs valors:

θ1 pot treballar de 0º a 180º, on 0º seria mirant a mà esquerra, 90º estaria paral·lel al vidre

frontal de la campana i 180 graus estaria mirant a mà dreta.

θ2 pot treballar de -90º a 90º, on -90 graus significaria posar el braç paral·lel al terra cap

enrere (la qual cosa representa un moviment impossible per a la fisiologia humana) i 90º

significaria posar el braç paral·lel al terra endavant (el qual seria un moviment quotidià) la

qual cosa implica que no podríem inclinar el braç per sobre de de tenir-lo paral·lel al terra,

però tenint en compte l’entorn en el que treballem, tampoc és necessari.

θ3 treballarà de 0º a 180º, on 0º voldria dir tenir l’avantbraç paral·lel al braç i 180º seria tenir-

lo igualment paral·lel però en sentit contrari (el qual també representa un moviment

impossible per a la fisiologia humana). Això implicaria que no podríem doblegar el colze

enrere, la qual cosa no ens suposa cap impediment real.

De la mateixa manera que amb l’apartat anterior, les equacions resultants, son massa

extenses per a ser plasmades a paper, però les podrem trobar dins el codi de l’Arduino.

B. PROGRAMA

B.1. Codi Comentat

//incloem una llibreria per a cada sensor

#include <MPU6050_tockn0.h>

#include <MPU6050_tockn1.h>

#include <MPU6050_tockn2.h>

#include <MPU6050_tockn3.h>

#include <Wire.h>

#include <VarSpeedServo.h>

//enllacem cada dispositiu amb les comandes que utilitza la seva llibreria

MPU60500 mpu60500(Wire);

MPU60501 mpu60501(Wire);

MPU60502 mpu60502(Wire);

MPU60502 mpu60503(Wire);

//variable que utilitzarem per controlar cada quan executem el programa

long timer = 0;

//variable que utilitzarem perquè els sensors només mostrin els seus valors un cop

per cicle

bool sensor = false;

//variable que utilitzarem perquè els càlculs només s'executin un cop per cicle

bool calcul = false;

//adreça del multiplexor TCA9548A

#define TCAADDR 0x70

//subrutina per escollir de quin canal llegeix el multiplexor

void tcaselect(uint8_t i)

{

if (i > 7) return;

Wire.beginTransmission(TCAADDR);

Wire.write(1 << i);

Wire.endTransmission();

}

//definim els servomotors

VarSpeedServo espatlla;

VarSpeedServo colze;

VarSpeedServo canell;

VarSpeedServo pinca;

VarSpeedServo esquena;

VarSpeedServo ma;

//definim les variables que utilitzarà la subrutina de càlcul

const float pi = 3.14159265359;

float theta1;

float theta2;

float theta3;

float theta5;

float X;

float Y;

float Z;

float R;

float R12;

float R1;

float R2;

float R3;

float R4;

long R5;

float S;

float T;

int L1 = 310;

int L2 = 80;

int a2 = 240;

int a3 = 300;

int L5 = 240;

float teta1;

float teta2;

float teta3;

float teta4;

float teta5;

float Axy;

float Az;

void setup()

{

//enllacem cada servomotor a un PIN PWM de l'Arduino

pinca.attach(3);

canell.attach(5);

colze.attach(6);

espatlla.attach(9);

esquena.attach(10);

ma.attach(11);

//declarem el pin 4 com a entrada

pinMode(4, INPUT);

//iniciem el port sèrie i l'I²C

Serial.begin(9600);

Wire.begin();

//calibrem cada giroscopi cada cop que iniciem el programa

tcaselect(0);

mpu60500.begin();

mpu60500.calcGyroOffsets(true);

tcaselect(1);

mpu60501.begin();

mpu60501.calcGyroOffsets(true);

tcaselect(2);

mpu60502.begin();

mpu60502.calcGyroOffsets(true);

tcaselect(3);

mpu60503.begin();

mpu60503.calcGyroOffsets(true);

//definim una posició inicial pel braç

esquena.write(0, 30, false);

espatlla.write(90, 30, false);

colze.write(90, 30, false);

canell.write(90, 30, false);

ma.write(0, 30, false);

pinca.write(90, 30, false);

}

void loop()

{

//el programa executa contínuament la subrutina que llegeix els valors que ens

arriben dels sensors

adquirir_dades();

//executem aqueta part del codi al inici de cada cicle

if ((millis() - timer > 0) && (millis() - timer < 1000) && sensor == false)

{

//executa la subrutina que imprimeix els valors llegits anteriorment pel canal

sèrie per ajudar a l'usuari a poder "debugar" amb més facilitat

imprimir_sensors();

//fem que la comanda anterior s'executi només 1 cop per cicle

sensor = true;

}

//executem aqueta part del codi quan hagi passat 1 segon

else if ((millis() - timer > 1000) && (millis() - timer < 4000) && calcul ==

false)

{

//executa | la | subrutina | que | calcula | els | valors | dels | angles | que | s'han | de

transmetre a cada articulació

calculs();

//executa la subrutina que imprimeix els valors calculats a la subrutina void

calculs() pel canal sèrie per ajudar a l'usuari a poder "debugar" amb més

facilitat

imprimir_valors();

//fem que les comandes anteriors s'executin només 1 cop per cicle

calcul = true;

//executa la subrutina que transmet els angles adients als servomotors

motors();

}

//executem aqueta part del codi quan hagin passat 4 segons

else if ((millis() - timer > 4000))

{

//fem reset al comptador i a les variables booleanes a fi de poder tornar a

executar el programa.

timer = millis();

sensor = false;

calcul = false;

}

}

void adquirir_dades()

{

tcaselect(0);

mpu60500.update();

tcaselect(1);

mpu60501.update();

tcaselect(2);

mpu60502.update();

tcaselect(3);

mpu60503.update();

}

void motors()

{

//cada servo executa l'angle que li pertoca. Li sumem un offset que depèn de la

posició inicial del servo.

int angle1 = teta1 + 0;

int angle2 = teta2 + 90;

int angle3 = teta3 + 90;

int angle4 = teta4 + 90;

int angle5 = teta5 + 0;

esquena.write(angle1, 30, false);

espatlla.write(angle2, 30, false);

colze.write(angle3, 30, false);

canell.write(angle4, 30, false);

ma.write(angle5, 30, false);

//obrim i tanquem la pinça en funció del polsador

if (digitalRead(4) == HIGH)

{

pinca.write(90, 30, false);

}

else

{

pinca.write(135, 30, false);

}

}

void imprimir_sensors()

{

Serial.println(' ');

Serial.print("Sensor 0: "); Serial.println(mpu60500.getAngleX());

Serial.println(' ');

Serial.print("Sensor 1: "); Serial.println(mpu60501.getAngleX());

Serial.println(' ');

Serial.print("Sensor 2: "); Serial.println(mpu60502.getAngleX());

Serial.println(' ');

Serial.print("Sensor 3: "); Serial.println(mpu60503.getAngleX());

Serial.println(' ');

}

void calculs()

{

//llegim | els | valors | dels | sensors | i | hi | afegim | un | offset | als | angles | perquè

s’adeqüin a la direcció original del model matricial

//theta1 és la lectura del sensor de l'esquena

int theta1_offset = 90;

theta1 = (mpu60500.getAngleX() + theta1_offset) * pi / 180;

//theta2 és la lectura del sensor de l'espatlla

int theta2_offset = -0;

theta2 = (-mpu60501.getAngleX() + theta2_offset) * pi / 180;

//theta3 és la lectura del sensor del colze

int theta3_offset = -0;

theta3 = (mpu60501.getAngleX() - mpu60502.getAngleX() + theta3_offset) * pi /

180;

//theta5 és la lectura del sensor de la mà int theta5_sensivility = 90 / 80;

theta5 = (mpu60503.getAngleX() * theta5_sensivility) * pi / 180;

//calcules la posició X, Y i Z de la punta de la pinça

X = +L2 * sin(theta1) - L5 * cos(theta3) * cos(-theta2 - theta3 - pi / 2) *

cos(theta1) * sin(theta2) - L5 * cos(theta3) * sin(-theta2 - theta3 - pi / 2) *

cos(theta1) * cos(theta2) + a3 * cos(theta3) * cos(theta1) * cos(theta2) - L5 *

sin(theta3) * cos(-theta2 - theta3 - pi / 2) * cos(theta1) * cos(theta2) + L5 *

sin(theta3) * sin(-theta2 - theta3 - pi / 2) * cos(theta1) * sin(theta2) - a3 *

sin(theta3) * cos(theta1) * sin(theta2) + a2 * cos(theta1) * cos(theta2);

Y = -L2 * cos(theta1) - L5 * cos(theta3) * cos(-theta2 - theta3 - pi / 2) *

sin(theta1) * sin(theta2) - L5 * cos(theta3) * sin(-theta2 - theta3 - pi / 2) *

sin(theta1) * cos(theta2) + a3 * cos(theta3) * sin(theta1) * cos(theta2) - L5 *

sin(theta3) * cos(-theta2 - theta3 - pi / 2) * sin(theta1) * cos(theta2) + L5 *

sin(theta3) * sin(-theta2 - theta3 - pi / 2) * sin(theta1) * sin(theta2) - a3 *

sin(theta3) * sin(theta1) * sin(theta2) + a2 * sin(theta1) * cos(theta2);

Z = L5 * cos(theta2) * cos(theta3) * cos(-theta2 - theta3 - pi / 2) - L5 *

cos(theta2) * sin(-theta2 - theta3 - pi / 2) * sin(theta3) + a3 * cos(theta2) *

sin(theta3) - L5 * cos(theta3) * sin(-theta2 - theta3 - pi / 2) * sin(theta2) +

a3 | * | cos(theta3) | * | sin(theta2) | - | L5 | * | cos(-theta2 | - | theta3 | - | pi | / 2) | *

sin(theta2) * sin(theta3) + a2 * sin(theta2) + L1;

teta1 = theta1 * 180 / pi;

teta2 = theta2 * 180 / pi;

teta3 = theta3 * 180 / pi;

//si X és més gran que 350 establirem que X = 350 i recalcularem el valor dels

angles teta1, teta2 i teta 3

if (X > 350)

{

X = 350;

teta1 = atan(Y / 350) + asin(80 / sqrt( pow(350, 2) + pow(Y, 2)));

teta1 = teta1 * 180 / pi;

Axy = sqrt(pow(350, 2) + pow(Y, 2) - pow(L2, 2));

Az = Z - 310;

teta2 = atan(((-pow(Axy, 2) * Az - pow(Az, 3) + 480 * Axy * Az + sqrt(-pow(Axy

, 6) - 2 * pow(Axy , 4) * pow(Az , 2) - pow(Axy , 2) * pow(Az , 4) + 1440 *

pow(Axy , 5) + 1920 * pow(Axy , 3) * pow(Az , 2) + 480 * Axy * pow(Az , 4) -

568800 * pow(Axy , 4) - 396000 * pow(Axy , 2) * pow(Az , 2) - 57600 * pow(Az ,

4) - 6912000 * pow(Axy , 3) - 31104000 * Axy * pow(Az , 2) + 51204960000 *
pow(Axy | , | 2) | + | 10368000000 | * | pow(Az | , | 2) | - | 11041920000000 | * | Axy | +

727833600000000) - 25200 * Az) / (pow(Axy , 2) + pow(Az , 2) - 480 * Axy +

57600)) / ((pow(Axy , 2) + pow(Az , 2) + (-pow(Axy , 2) * Az - pow(Az , 3) +

480 * Axy * Az + sqrt(-pow(Axy , 6) - 2 * pow(Axy , 4) * pow(Az , 2) - pow(Axy

, 2) * pow(Az , 4) + 1440 * pow(Axy , 5) + 1920 * pow(Axy , 3) * pow(Az , 2) +

480 * Axy * pow(Az , 4) - 568800 * pow(Axy , 4) - 396000 * pow(Axy , 2) *

pow(Az , 2) - 57600 * pow(Az , 4) - 6912000 * pow(Axy , 3) - 31104000 * Axy *

pow(Az , 2) + 51204960000 * pow(Axy , 2) + 10368000000 * pow(Az , 2) -

11041920000000 * Axy + 727833600000000) - 25200 * Az) * Az / (pow(Axy , 2) +

pow(Az , 2) - 480 * Axy + 57600) - 480 * Axy + 25200) / (Axy - 240)));

// | teta2 = teta2 * 180 / pi;

if (teta2 < 0)

{

teta2 = -teta2 * 180 / pi - 180;

}

else

{

teta2 = -teta2 * 180 / pi;

}

R12 = (pow(Axy, 2) + pow(Az, 2) - 480 * Axy - 720000 / 8);

R1 = R12 / 144000;

R2 = (pow(Axy, 2) * Az + pow(Az, 3) - 480 * Axy * Az + 25200 * Az);

R3 = ((144000 * Axy - 34560000) * (pow(Axy, 2) + pow(Az, 2) - 480 * Axy +

57600));

R4 = -pow(Axy, 6) - 2 * pow(Axy, 4) * pow(Az, 2) - pow(Axy, 2) * pow(Az, 4) +

1440 * pow(Axy, 5) + 1920 * pow(Axy, 3) * pow(Az, 2) + 480 * Axy * pow(Az, 4)

- 568800 * pow(Axy, 4) - 396000 * pow(Axy, 2) * pow(Az, 2) - 57600 * pow(Az,
4) - 6912000 * pow(Axy, 3) - 31104000 * Axy * pow(Az, 2) + 51204960000 *
pow(Axy, | 2) | + | 10368000000 | * | pow(Az, | 2) | - | 11041920000000 | * | Axy | +

727833600000000;

R5 = 480 * pow(Axy, 2) + 480 * pow(Az, 2) - 230400 * Axy + 27648000;

teta3 = atan(((1 / 480.0) * (R5) * (-pow(Axy, 2) * Az - pow(Az, 3) + 480 * Axy

* Az + sqrt(R4) - 25200.0 * Az) / R3 + R2 / (144000.0 * Axy - 34560000.0)) /

R1);

if (teta3 < 0)

{

teta3 = teta3 * 180 / pi + 180;

}

else

{

teta3 = teta3 * 180 / pi;

}

}

//si X és més petita que -350 establirem que X = -350 i recalcularem el valor

dels angles teta1, teta2 i teta 3

else if (X < -350)

{

X = -350;

teta1 = atan(350 / Y) + asin(80 / (sqrt(pow(Y , 2) + pow(350 , 2))));

teta1 = teta1 * 180 / pi + 90;

Axy = sqrt(pow(350 , 2) + pow(Y , 2) - pow(L2 , 2));

Az = Z - 310;

teta2 = atan(((-pow(Axy, 2) * Az - pow(Az, 3) + 480 * Axy * Az + sqrt(-pow(Axy

, 6) - 2 * pow(Axy , 4) * pow(Az , 2) - pow(Axy , 2) * pow(Az , 4) + 1440 *

pow(Axy , 5) + 1920 * pow(Axy , 3) * pow(Az , 2) + 480 * Axy * pow(Az , 4) -

568800 * pow(Axy , 4) - 396000 * pow(Axy , 2) * pow(Az , 2) - 57600 * pow(Az ,

4) - 6912000 * pow(Axy , 3) - 31104000 * Axy * pow(Az , 2) + 51204960000 *
pow(Axy | , | 2) | + | 10368000000 | * | pow(Az | , | 2) | - | 11041920000000 | * | Axy | +

727833600000000) - 25200 * Az) / (pow(Axy , 2) + pow(Az , 2) - 480 * Axy +

57600)) / ((pow(Axy , 2) + pow(Az , 2) + (-pow(Axy , 2) * Az - pow(Az , 3) +

480 * Axy * Az + sqrt(-pow(Axy , 6) - 2 * pow(Axy , 4) * pow(Az , 2) - pow(Axy

, 2) * pow(Az , 4) + 1440 * pow(Axy , 5) + 1920 * pow(Axy , 3) * pow(Az , 2) +

480 * Axy * pow(Az , 4) - 568800 * pow(Axy , 4) - 396000 * pow(Axy , 2) *

pow(Az , 2) - 57600 * pow(Az , 4) - 6912000 * pow(Axy , 3) - 31104000 * Axy *

pow(Az , 2) + 51204960000 * pow(Axy , 2) + 10368000000 * pow(Az , 2) -

11041920000000 * Axy + 727833600000000) - 25200 * Az) * Az / (pow(Axy , 2) +

pow(Az , 2) - 480 * Axy + 57600) - 480 * Axy + 25200) / (Axy - 240)));

if (teta2 < 0)

{

teta2 = -teta2 * 180 / pi - 180;

}

else

{

teta2 = -teta2 * 180 / pi;

}

R12 = (pow(Axy, 2) + pow(Az, 2) - 480 * Axy - 720000 / 8);

R1 = R12 / 144000;

R2 = (pow(Axy, 2) * Az + pow(Az, 3) - 480 * Axy * Az + 25200 * Az);

R3 = ((144000 * Axy - 34560000) * (pow(Axy, 2) + pow(Az, 2) - 480 * Axy +

57600));

R4 = -pow(Axy, 6) - 2 * pow(Axy, 4) * pow(Az, 2) - pow(Axy, 2) * pow(Az, 4) +

1440 * pow(Axy, 5) + 1920 * pow(Axy, 3) * pow(Az, 2) + 480 * Axy * pow(Az, 4)

- 568800 * pow(Axy, 4) - 396000 * pow(Axy, 2) * pow(Az, 2) - 57600 * pow(Az,
4) - 6912000 * pow(Axy, 3) - 31104000 * Axy * pow(Az, 2) + 51204960000 *
pow(Axy, | 2) | + | 10368000000 | * | pow(Az, | 2) | - | 11041920000000 | * | Axy | +

727833600000000;

R5 = 480 * pow(Axy, 2) + 480 * pow(Az, 2) - 230400 * Axy + 27648000;

teta3 = atan(((1 / 480.0) * (R5) * (-pow(Axy, 2) * Az - pow(Az, 3) + 480 * Axy

* Az + sqrt(R4) - 25200.0 * Az) / R3 + R2 / (144000.0 * Axy - 34560000.0)) /

R1);

if (teta3 < 0)

{

teta3 = teta3 * 180 / pi + 180;

}

else

{

teta3 = teta3 * 180 / pi;

}

}

else

{

teta1 = theta1;

teta2 = theta2;

teta3 = theta3;

teta1 = teta1 / pi * 180;

teta2 = teta2 / pi * 180;

teta3 = teta3 / pi * 180;

}

teta1 = teta1 / 180 * pi;

teta2 = teta2 / 180 * pi;

teta3 = teta3 / 180 * pi;

R = +L2 * sin(teta1) | - L5 * cos(teta3) | * cos(-teta2 - teta3 - pi / 2) *

cos(teta1) * sin(teta2) - L5 * cos(teta3) * sin(-teta2 - teta3 - pi / 2) *

cos(teta1) * cos(teta2) + a3 * cos(teta3) * cos(teta1) * cos(teta2) - L5 *

sin(teta3) * cos(-teta2 - teta3 - pi / 2) * cos(teta1) * cos(teta2) + L5 *

sin(teta3) * sin(-teta2 - teta3 - pi / 2) * cos(teta1) * sin(teta2) - a3 *

sin(teta3) * cos(teta1) * sin(teta2) + a2 * cos(teta1) * cos(teta2);

S = -L2 * cos(teta1) - L5 * cos(teta3) * cos(-teta2 - teta3 - pi / 2) *

sin(teta1) * sin(teta2) - L5 * cos(teta3) * sin(-teta2 - teta3 - pi / 2) *

sin(teta1) * cos(teta2) + a3 * cos(teta3) * sin(teta1) * cos(teta2) - L5 *

sin(teta3) * cos(-teta2 - teta3 - pi / 2) * sin(teta1) * cos(teta2) + L5 *

sin(teta3) * sin(-teta2 - teta3 - pi / 2) * sin(teta1) * sin(teta2) - a3 *

sin(teta3) * sin(teta1) * sin(teta2) + a2 * sin(teta1) * cos(teta2);

T = L5 * cos(teta2) * cos(teta3) * cos(-teta2 - teta3 - pi / 2) - L5 *

cos(teta2) * sin(-teta2 - teta3 - pi / 2) * sin(teta3) + a3 * cos(teta2) *

sin(teta3) - L5 * cos(teta3) * sin(-teta2 - teta3 - pi / 2) * sin(teta2) + a3 *

cos(teta3) * sin(teta2) - L5 * cos(-teta2 - teta3 - pi / 2) * sin(teta2) *

sin(teta3) + a2 * sin(teta2) + L1;

//finalment obtenim els valors de tots els angles on teta1 equival al servo de

l'esquena, teta2 equival al servo de l'espatlla, teta3 equival al servo del

colze, teta4 equival al servo del canell i teta5 equival al servo de la rotació

de la mà

teta1 = teta1 / pi * 180;

teta2 = teta2 / pi * 180;

teta3 = teta3 / pi * 180;

teta4 = (teta2 + teta3);

teta5 = theta5;

theta1 = theta1 * 180 / pi;

theta2 = theta2 * 180 / pi;

theta3 = theta3 * 180 / pi;

}

void imprimir_valors()

{

//X, Y i Z són els valors de la posició de la punta de la pinça calculats a

partir dels valors dels angles directament llegits dels sensors

Serial.print("X: ");

Serial.println(X);

Serial.print("Y: ");

Serial.println(Y);

Serial.print("Z: ");

Serial.println(Z);

//R, S i T són els valors de la posició de la punta de la pinça calculats a

partir dels valors dels angles si aquests han hagut de ser re-calculats

Serial.print("R: ");

Serial.println(R);

Serial.print("S: ");

Serial.println(S);

Serial.print("T: ");

Serial.println(T);

Serial.println(" ");

Serial.print("Axy: ");

Serial.println(Axy);

Serial.print("Az: ");

Serial.println(Az);

Serial.println(" ");

Serial.print("R1: ");

Serial.println(R1);

Serial.print("R2: ");

Serial.println(R2);

Serial.print("R3: ");

Serial.println(R3);

Serial.print("R4: ");

Serial.println(R4);

Serial.print("R5: ");

Serial.println(R5);

Serial.println(" ");

//theta són els valors dels angles de cada una de les articulacions llegida

directament dels sensors

Serial.print("theta1: ");

Serial.println(theta1);

Serial.print("theta2: ");

Serial.println(theta2);

Serial.print("theta3: ");

Serial.println(theta3);

//teta són els valors dels angles de cada una de les articulacions després de

ser re-calculades

Serial.print("teta1: ");

Serial.println(teta1);

Serial.print("teta2: ");

Serial.println(teta2);

Serial.print("teta3: ");

Serial.println(teta3);

Serial.print("teta4: ");

Serial.println(teta4);

Serial.print("teta5: ");

Serial.println(teta5);

Serial.println(' ');

}

Fig. 24: Esquema del braç robòtic amb vectors

θ | d | a | α | H
1 | q1 | L1 | 0 | 90º | 90º
2 | q2 | L2 | a2 | 0 | 0
3 | q3 | 0 | a3 | 0 | 0
4 | q4 | 0 | 0 | -90º | -90º
5 | q5 | L5 | 0 | 0 | 0

Taula 1: Taula de Denavit Hartenberg del braç robòtic

C. SIMULACIÓ INFORMÀTICA DEL BRAÇ

C.1. Simulació del braç amb Matlab i Robotics Toolbox

Tal i com hem vist a l’apartat 3 Descripció del programa, l’Arduino haurà de calcular,

mitjançant cinemàtica directe, la posició de la punta del braç, i si s’escau, mitjançant

cinemàtica inversa, tornar a calcular els valors dels angles resultants.

Per a realitzar aquest segon càlcul, habitualment, utilitzaríem un “solver”, malauradament,

no existeixen llibreries per a Arduino capaces de realitzar operacions amb aquest nivell de

complexitat.

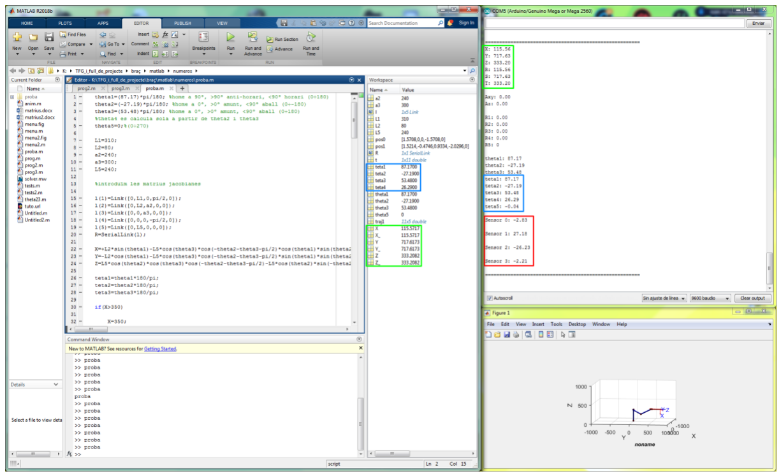
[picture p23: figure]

Fig. 25: Simulació en paral·lel entre Matlab i Arduino sense tornar a calcular els angles

Tal i com podem veure a l’annex A.2. Modelització matemàtica del braç, hem hagut de

buscar les equacions de cinemàtica inversa, ja aïllades, a fi que l’Arduino les pugui

processar correctament.

La simulació realitzada amb Matlab, està realitzada amb l’ajuda de la “Robotics Toolbox” la

qual és fàcil d’utilitzar però alhora et permet assolir alts nivells de complexitat si és requerit.

Per a poder utilitzar aquesta eina es requereix proporcionar-li al Matlab la taula de Denavit

Hartenberg corresponent al braç robòtic.

Nosaltres a la simulació li hem subministrat uns valors a l’atzar els quals representarien els

valors llegits pels hipotètics giroscopis. El Matlab ha calculat la posició de la punta del braç i

en el cas que sortís fora de la suposada campana, torna a calcular els valors dels angles,

imposant un nou valor per a la variable X.

El Matlab, per a fer aquest segon càlcul dels nous valors dels angles, ho ha fet de dos

maneres, utilitzant el “solver” intern de Matlab i utilitzant les equacions de la cinemàtica

inversa a fi de poder comparar si els resultats obtingut per ambdós mètodes és el mateix. Si

així fos, voldria dir que l’Arduino és capaç de realitzar els càlculs sense equivocar-se, ja que

podria obtenir el mateix resultat que amb un “solver” sense disposar d’aquest.

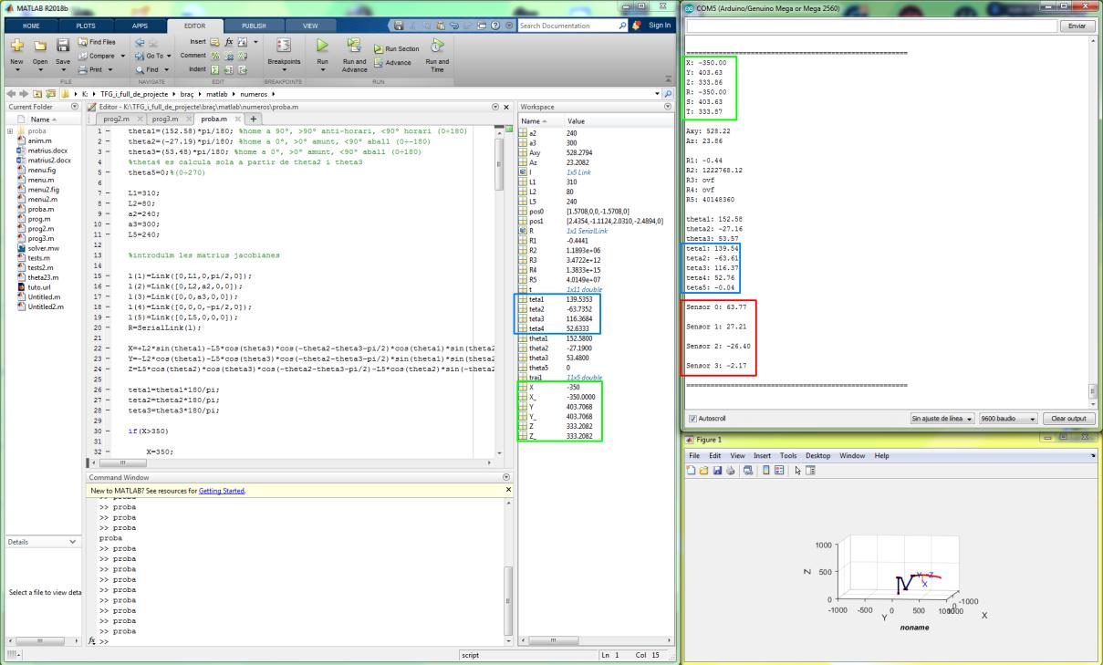
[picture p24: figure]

Fig. 26: Simulació en paral·lel entre Matlab i Arduino tornant a calcular els angles

A la figura 32 podem veure una simulació en paral·lel entre el Matlab i l’Arduino on els

valors “theta” són els que han llegit els sensors i “teta” són els valors després de tornar a

calcular (el mateix valor en cas que no necessitem segon càlcul) i podem veure que com

que el valor de X és dins del rang de ± 350 no hem necessitat segon càlcul per tant, els

valors de les “thetes” i les “tetes” coincideixen.

En canvi la figura 33 podem veure que com que X en una primera instància estaria fora del

rang de ± 350, per tant, se li adjudica aquest valor i en fa el 2n càlcul dels angles, per això

podem veure que els valors de “theta” i “teta” no coincideixen.

Observant aquests dos casos podem coincidir en què el programa funciona correctament.

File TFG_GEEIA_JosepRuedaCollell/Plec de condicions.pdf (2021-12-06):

# Treball final de grau

Estudi: Grau en Enginyeria Electrònica | Industrial i
. | Automàtica

## Títol:

# Disseny d’un braç robòtic controlat per un guant electrònic

## Document 3: Plec de condicions

## Alumne: Josep Rueda Collell

## Tutor: Miquel Rustullet Reñe Departament: Enginyeria Elèctrica, Electrònica i Automàtica Àrea: Enginyeria de Sistemes i Automàtica

## Convocatòria: Juny/2019

Disseny d’un braç robòtic controlat per un guant electrònic | Plec de condicions

INDEX:

### 1. INTRODUCCIÓ

El present document conté les especificacions particulars i les condicions a les que s’haurà

d’ajustar l’elaboració i execució del projecte.

### 1.1. Objecte del plec de condicions

El present plec de condicions constitueix el conjunt d’instruccions, normes, especificacions,

condicions tècniques i econòmiques i les disposicions legals que defineixen tots els requisits

tècnics per dur a terme la implementació del braç robòtic.

S’establirà la prioritat de la documentació i el grau de validesa.

En cas de no complir les normes i especificacions que s’indiquen dins el projecte, l’enginyer

dissenyador del projecte no es farà càrrec dels problemes que puguin aparèixer.

### 1.2. Documents contractuals i informatius

Es consideraran com a documents contractuals els plànols, la memòria, el plec de

condicions i l’estat d’amidaments. Es considerarà com a document informatiu el pressupost.

### 1.3. Compatibilitat entre documents

Per establir un ordre de prioritat entre documents es prendrà com a primer document de

referència els plànols, seguit de la memòria, el plec de condicions, l’estat d’amidaments i per

últim el pressupost.

### 2. DISPOSICIONS TÈCNIQUES

En aquest capítol es mencionarà totes les especificacions tècniques a tenir en compte tals

com les normatives, els reglaments i organismes que puguin estar relacionades amb el

projecte.

### 2.1. Reglament

Reglament Electrònic de Baixa tensió (Reial Decret 842/2002, 2 d’agost). Es classifica la

tensió dels projecte com a tensió usual amb corrent alterna de 230V. Caldrà complir totes

les instruccions tècniques que reguli aquest reglament.

### 2.2. Normes

Caldrà tenir present les normes UNE que fan referencia a les proteccions que ha de tenir un

aparell elèctric. En concret, la UNE 20314 la qual fa referència a les normes de seguretat

d’aparells elèctrics per a baixa tensió i protecció contra els xocs elèctrics i la UNE 20324 la

qual explica el grau de protecció que hauran de tenir els embolcalls del material elèctric de

baixa tensió.

Es compliran els estàndards de la normativa ISO 9000 de qualitat i gestió continua de la

qualitat.

### 3. CONDICIONS TÈCNIQUES

Si es vol garantir el bon funcionament d’aquest projecte s’haurà de complir estrictament amb

les condicions tècniques especificades en els plànols, l’estat d’amidaments i la memòria.

L’enginyer tècnic autor del projecte no es farà responsable del mal funcionament del

projecte si alguna de les condicions tècniques esmentades no són les corresponents.

### 3.1. Material

S’haurà de complir estrictament amb tot el material indicat en els altres documents, en

especial amb les dimensions dels components del braç a fi que el programa no quedi

inservible.

Es donarà una orientació del format de la caixa on es muntarà la PCB i l’Arduino, la font

d’alimentació, els transformadors, el cablejat i les connexions, tot i que la forma i distribució

final és oberta al disseny que es cregui més convenient. Això no exclou de complir totes les

normes de seguretat que s’indiquen.

Els components electrònics hauran de ser estrictament els esmentats en la resta de

documents, si es requereix fer un canvi d’algun element equivalent s’haurà de consultar al

tècnic que ha desenvolupat el projecte.

### 3.2. Muntatge

Per què el braç funcioni correctament s’ha de complir la informació descrita a la memòria i

als plànols, referent a la fabricació.

La programació de l’Arduino haurà de seguir el procediment descrit a la memòria on hi ha

detalls importants sobre la implementació del codi.

Per a fer sortir el cable de l’alimentació de la caixa elèctrica, així com els cables DuPond

l’operari encarregat del muntatge de la caixa, utilitzarà els conseqüents passa-murs els quals estrangulen els cables, de tal manera que es pugui evitar que estirades accidentals

puguin desconnectar o malmetre els components interns de la caixa.

Els cables DuPond varien en la seva longitud segons el fabricant, per tant, si l’operari

requereix realitzar una unió entre 2 cables DuPond de forma segura, utilitzarà tub

termoretràctil. Tenint en compte la geometria dels cables DuPond, aconseguirem una unió

fiable i segura. Si més endavant es volguessin fer ampliacions o canviar algun cable, només

s’hauria de tallar el tub termoretràctil a fi de desconnectar dos cables, la qual cosa facilitaria

molt la tasca. Tanmateix, l’operari és lliure d’utilitzar qualsevol cable sempre que es puguin

connectar correctament amb els dispositius i que puguin suportar més de 3 A tenint en

compte la normativa per a instalacions de baixa tensió.

Tant el cables DuPond dels sensors i els del polsador del guant com els dels servomotors

del braç, es podran unir a l’estructura utilitzant la unió que l’instal·lador trobi més adient. Cal

recordar que els cables han de donar joc a les articulacions a fi de evitar estrebades.

L’operari encarregat de construir el guant, podrà utilitzar la unió que cregui més adient entre

el guant i els sensors, però és de suma importància que l’eix de gir dels sensors quedi

paral·lel o perpendiculars al pla del terra segons ho indica la memòria.

### 4. DISPOSICIONS GENERALS

El disseny s’ha elaborat per cobrir exclusivament les necessitats descrites a la memòria. En

cas de designar-se a un altre fi, o si és necessari realitzar algun tipus de modificació,

l’enginyer dissenyador del projecte no es farà càrrec dels problemes que puguin aparèixer.

### 4.1. Administratives o legals

La maquinària i components utilitzats han d’estar lliures de qualsevol error o defecte de

disseny, material i/o construcció. L’enginyer dissenyador queda lliure de responsabilitat dels

danys que pugui ocasionar la utilització de la maquinària i components amb algun tipus de

defecte de fabricació.

La garantia del sistema és vàlida sempre que totes les operacions de manteniment del

sistema siguin dutes a terme per personal qualificat i experimentat.

En cas de que sigui una empresa externa la que s’encarregui de la instal·lació, aquesta

haurà de complir les normes d’execució i respectar els terminis temporals establerts amb el

client.

El cost de l’elaboració del projecte s’abonarà un cop s’entregui aquest. Si la proposta del

projecte segueix endavant, es seguirà el descrit a la resta de documents, amb el cost descrit

al document pressupost. Qualsevol modificació comportarà un nou pressupost i una nova

acceptació de condicions.

El projecte s’entregarà en un fitxer ZIP el qual contindrà tots els documents necessaris per a

realitzar-lo.

### 4.2. Garantia

Un cop realitzada la implementació d’aquest projecte té una garantia amb validesa de dos

anys. Desprès d’aquest termini, el projectista no es farà càrrec de qualsevol desperfecte o

mal funcionament que hagi pogut sorgir al braç.

### 4.3. Pagament

El pagament es realitzarà quan s’hagi entregat el projecte al client amb tots els documents

firmats degudament. Aquest es realitzarà mitjançant una transferència bancària.

Josep Rueda Collell

Graduat en enginyeria Electrònica Industrial i Automàtica.

Girona, 6 de juny de 2019

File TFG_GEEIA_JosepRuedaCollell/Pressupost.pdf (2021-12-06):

# Treball final de grau

## Estudi: Grau en Enginyeria Electrònica Industrial i

. | Automàtica

### Títol:

# Disseny d’un braç robòtic controlat per un guant electrònic

### Document 5: Pressupost

### Alumne: Josep Rueda Collell

### Tutor: Miquel Rustullet Reñe Departament: Enginyeria Elèctrica, Electrònica i Automàtica Àrea: Enginyeria de Sistemes i Automàtica

### Convocatòria: Juny/2019

Disseny d’un braç robòtic controlat per un guant electrònic | Pressupost

ÍNDEX:

1. | PREUS UNITARIS | 2
1.1. | Material | 2
1.2. | Treball | 2
2. | PRESSUPOST PARCIAL | 3
2.1. | Implementació electrònica del braç i mà | 3
2.2. | Implementació electrònica del guant i processador | 3
2.3. | Implementació programa | 4
2.4. | Posada en funcionament | 4
3. | PRESSUPOST TOTAL | 5
A.1. | Cost del projecte | 6

### 1. PREUS UNITARIS

### 1.1. Material

Descripció | Cost unitari €/u
Robot Digital Servo RDS5160 | 25,31
Robot Digital Servo RDS3135 | 16,64
Robot Digital Servo RDS3218 | 8,23
Digital Servo HS-785HB | 34,00
Cable DuPont Mascle-Mascle | 0,08
Cable DuPont Mascle-Femella | 0,08
Transformador DC-DC XH-M401 | 6,00
Arduino Uno | 20,00
Giroscopi MPU-6050 | 4,00
Multiplexor TCA9548A | 5,00
Cable DuPont Mascle-Mascle | 0,08
Cable DuPont Mascle-Femella | 0,08
Transformador DC-DC XH-M401 | 6,00
Font GHB 12V ESP127 | 50,00
Polsador B3F | 0,245
Placa fibra doble cara 80x120 mm | 4,25
Nucli de ferrita Vk200 | 10,00
Caixa elèctrica 746-903 Altech 450 mm x 300 mm x 94 mm | 137,94

### 1.2. Treball

Treball
Descripció | Cost unitari €/h
Enginyer | 30,00
Oficial de primera | 25,00
Mà d'obra | 20,00

### 2. PRESSUPOST PARCIAL

### 2.1. Implementació electrònica del braç i mà

Descripció | Quantitat C. unit.€/u Import €
Robot Digital Servo RDS5160 | 1 | 25,31 | 25,31
Robot Digital Servo RDS3135 | 1 | 16,64 | 16,64
Robot Digital Servo RDS3218 | 2 | 8,23 | 16,46
Digital Servo HS-785HB | 2 | 34,00 | 68,00
Cable DuPont Mascle-Mascle | 40 | 0,08 | 3,20
Cable DuPont Mascle-Femella | 80 | 0,08 | 6,40
DC-DC XH-M401 | 3 | 6,00 | 18,00
h Connectar i soldar els diferents components | 2 | 20,00 | 40,00
h Enginyer | 2 | 30,00 | 60,00
h Oficial de primera | 2 | 25,00 | 50,00
| | SUBTOTAL | 304,01 €

### 2.2. Implementació electrònica del guant i processador

Descripció | Quantitat C. unit.€/u Import €
Arduino Uno | 1 | 20,00 | 20,00
Giroscopi MPU-6050 | 4 | 4,00 | 16,00
Multiplexor TCA9548A | 1 | 5,00 | 5,00
Cable DuPont Mascle-Mascle | 40 | 0,08 | 3,20
Cable DuPont Mascle-Femella | 80 | 0,08 | 6,40
Transformador DC-DC XH-M401 | 1 | 6,00 | 6,00
Font GHB 12V ESP127 | 1 | 50,00 | 50,00
Polsador B3F | 1 | 0,245 | 0,245
Placa fibra doble cara 80x120 mm | 1 | 4,25 | 4,25
Nucli de ferrita Vk200 | 1 | 10,00 | 10,00
Caixa eléctrica 746-903 Altech 450 mm x 300 mm x 94 mm | 1 | 137,94 | 137,94
h Connectar i soldar dels diferents components | 2 | 20,00 | 40,00
h Enginyer | 2 | 30,00 | 60,00
h Oficial de primera | 2 | 25,00 | 50,00
| | SUBTOTAL | 409,04 €

### 2.3. Implementació programa

Descripció | Quantitat C. unit.€/u | Import €
h Enginyer | 20 | 30,00 | 600,00€
| | SUBTOTAL | 600,00 €

### 2.4. Posada en funcionament

Descripció | Quantitat C. unit.€/u | Import €
h Enginyer | 4 | 30,00 | 120,00€
h Oficial de primera | 4 | 25,00 | 100,00€
| | SUBTOTAL | 220,00 €

### 3. PRESSUPOST TOTAL

Descripció | Import
Implementació electrònica del braç i mà | 304,01 €
Implementació electrònica del guant i processador | 409,04 €
Implementació programa | 600,00 €
Posada en funcionament | 220,00 €
BASE IMPOSABLE | 1.533,05 €
21% IVA | 321,94 €
TOTAL | 1.854,99 €

Josep Rueda Collell

Graduat en enginyeria Electrònica Industrial i Automàtica.

Girona, 6 de juny de 2019

A.1. Cost del projecte

Descripció | Hores | Cost (€/h) | Import
Projectista | 400 | 10,00 4.000,00 €
| | TOTAL | 4.000,00 €

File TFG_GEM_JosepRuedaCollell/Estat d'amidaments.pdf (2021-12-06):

# Treball final de grau

## Estudi: Grau en Enginyeria Mecànica

### Títol:

# Disseny d’un braç robòtic controlat per un guant electrònic

### Document 4: Estat d’Amidaments

### Alumne: Josep Rueda Collell

### Tutor: Narcís Gascons Clarió Departament: Enginyeria Mecànica i de la Construcció Industrial Àrea: Enginyeria Mecànica

### Convocatòria: Juny/2019

Disseny d’un braç robòtic controlat per guant electrònic | Estat d’Amidaments

ÍNDEX:

### 1. Implementació mecànica del braç

Descripció | Material | Plànol | Unit. | Quantitat
Tub perfil rectangular 45 x 20 x 1,2 | Alumini | | mm | 240
Tallar i trepanar | | | h | 0,5
Tub perfil rectangular 54,76 x 18,78 x 2,04 | Alumini | | mm | 228,4
Tallar i trepanar | | | h | 0,5
Prisma 42,6 x 17,6 x 24 | PLA | | u | 2
Prisma 52,8 x 16,82 x 24 | PLA | | u | 2
Servo-Block Hitec 637118 | Alumini | | u | 2
Suport Espatlla (Peça de fabricació) | Alumini | 7 | u | 1
Base Braç (Peça de fabricació) | PLA | 6 | u | 1
Base Canell (Peça de fabricació) | PLA | 9 | u | 1
DIN 7981 Cargol Auto-roscant Cap Rodó Creu M4 x 6,5 | PLA | | u | 48
DIN 7985 Cargol Cap Rodó Creu M3,5 x 12 | Acer | | u | 12
DIN 7985 Cargol Cap Rodó Creu M3,5 x 8 | Acer | | u | 4
Realitzar el muntatge de l'estructura del braç | | | h | 4
Enginyer | | | h | 4
Oficial de primera | | | h | 4

### 2. Implementació mecànica de la mà

Descripció | Material | Plànol | Unit. | Quantitat
Suport Mà (Peça de fabricació) | PLA | 5 | u | 1
Biela Dentada Øp = 10 m=1,5 (Peça de fabricació) | PLA | 4 | u | 2
Biela (Peça de fabricació) | PLA | 4 | u | 4
Suport Goma (Peça de fabricació) | PLA | 3 | u | 2
Prisma Goma 10 x 40 x 40 | Cautxú Elast. | | u | 2
Tallar | | | h | 0,1
DIN 7985 Cargol Cap Rodó Creu M3,5 x 12 | Acer | | u | 8
Barilla DIN 14021 Ø 3,5 x 40 | Acer | | u | 4
Tallar | | | h | 0,1
Implementació i muntatge de la Mà | | | h | 2
Enginyer | | | h | 2
Oficial de primera | | | h | 2

### 3. Implementació mecànica del guant

Descripció | Material | Plànol | Unit. | Quantitat
Tela | Cotó Fi | | m
| | | 2 | 1
Tancament Velcro 25 x 300 | Niló | | u | 1
Oficial de primera | | | h | 1

### 4. Implementació electrònica del braç i mà

Descripció | Unit. | Quantitat
Robot Digital Servo RDS5160 | u | 1
Robot Digital Servo RDS3135 | u | 1
Robot Digital Servo RDS3218 | u | 2
Digital Servo HS-785HB | u | 2
Cable DuPont Mascle-Mascle | u | 40
Cable DuPont Mascle-Femella | u | 80
DC-DC XH-M401 | u | 3
Connectar i soldar els diferents components | h | 2
Enginyer | h | 2
Oficial de primera | h | 2

### 5. Implementació electrònica del guant i processador

Descripció | Unit. | Quantitat
Arduino Uno | u | 1
MPU-6050 | u | 4
Multiplexor I2C TCA9548A | u | 1
Cable DuPont Mascle-Mascle | u | 40
Cable DuPont Mascle-Femella | u | 80
DC-DC XH-M401 | u | 1
Font Compaq ESP127 | u | 1
Polsador B3F | u | 1
Placa fibra doble cara 80x120 mm | u | 1
Nucli de ferrita Vk200 | u | 1
Caixa elèctrica 746-903 Altech 450 x 300 x 94 mm | u | 1
Connectar i soldar dels diferents components | h | 2
Enginyer | h | 2
Oficial de primera | h | 2

### 6. Implementació programa

Descripció | Unit. | Quantitat
Enginyer | h | 20

### 7. Posada en funcionament

Components mecànics de la Mà
Descripció | Unit. | Quantitat
Enginyer | h | 4
Oficial de primera | h | 4

Josep Rueda Collell

Graduat en Enginyeria Mecànica.

Girona, 6 de juny de 2019

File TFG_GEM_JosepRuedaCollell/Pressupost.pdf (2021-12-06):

# Treball final de grau

## Estudi: Grau en Enginyeria Mecànica

### Títol:

# Disseny d’un braç robòtic controlat per un guant electrònic

### Document 5: Pressupost

### Alumne: Josep Rueda Collell

### Tutor: Narcís Gascons Clarió Departament: Enginyeria Mecànica i de la Construcció Industrial Àrea: Enginyeria Mecànica

### Convocatòria: Juny/2019

Disseny d’un braç robòtic controlat per un guant electrònic | Pressupost

ÍNDEX:

ÍNDEX: | 1
1. | PREUS UNITARIS | 2
1.1. | Components mecànics | 2
1.2. | Components electrònics | 2
1.3. | Treball | 2
2. | PRESSUPOST PARCIAL | 4
2.1. | Implementació mecànica del braç | 4
2.2. | Implementació mecànica de la mà | 4
2.3. | Implementació mecànica del guant | 5
2.4. | Implementació electrònica del braç i mà | 5
2.5. | Implementació electrònica del guant i processador | 5
2.6. | Implementació programa | 6
2.7. | Posada en funcionament | 6
3. | PRESSUPOST TOTAL | 7
ANNEX AL PRESSUPOST | 8
A.1. | Cost del projecte | 9

### 1. PREUS UNITARIS

### 1.1. Components mecànics

Descripció | Material | Unitat | Cost unitari €/u
Tub perfil rectangular 45 x 20 x 1,2 | Alumini mm | 0,01
Tub perfil rectangular 54,76 x 18,78 x 2,04 | Alumini mm | 0,01
Prisma 42,6 x 17,6 x 24 | PLA | u | 15,00
Prisma 52,8 x 16,82 x 24 | PLA | u | 15,00
Servo-Block Hitec 637118 | Alumini | u | 35,37
Suport Espatlla (Peça de fabricació) | PLA | u | 30,00
Base Braç (Peça de fabricació) | PLA | u | 50,00
Base Canell (Peça de fabricació) | PLA | u | 30,00
DIN 7981 Cargol Auto-roscant Cap Rodó Creu M4 x 6,5 | Acer | u | 0,03
DIN 7985 Cargol Cap Rodó Creu M3,5 x 12 | Acer | u | 0,03
DIN 7985 Cargol Cap Rodó Creu M3,5 x 8 | Acer | u | 0,03
Suport Mà (Peça de fabricació) | PLA | u | 30,00
Biela Dentada Øp = 20 m=0,75(Peça de fabricació) | PLA | u | 10,00
Biela (Peça de fabricació) | PLA | u | 5,00
Suport Goma (Peça de fabricació) | PLA | u | 10,00
Prisma Goma 10 x 40 x 40 | Cautxú Elast. | u | 5,00
DIN 7985 Cargol Cap Rodó Creu M3,5 x 12 | Acer | u | 0,03
Barilla DIN 14021 Ø 3,5 x 40 | Acer | u | 0,03
Tela | Cotó Fi | m

2
14,00
Tancament Velcro 25 x 300 | Niló | u | 1,00

### 1.2. Components electrònics

Descripció | Unitat | Cost unitari €/u
Robot Digital Servo RDS5160 | u | 25,31
Robot Digital Servo RDS3135 | u | 16,64
Robot Digital Servo RDS3218 | u | 8,23
Digital Servo HS-785HB | u | 34,00
Cable DuPont Mascle-Mascle | u | 0,08
Cable DuPont Mascle-Femella | u | 0,08
Transformador DC-DC XH-M401 | u | 6,00
Arduino Uno | u | 20,00
Giroscopi MPU-6050 | u | 4,00
Multiplexor TCA9548A | u | 5,00
Cable DuPont Mascle-Mascle | u | 0,08
Cable DuPont Mascle-Femella | u | 0,08
Transformador DC-DC XH-M401 | u | 6,00
Font GHB 12V ESP127 | u | 50,00
Polsador B3F | u | 0,245
Placa fibra doble cara 80x120 mm | u | 4,25
Nucli de ferrita Vk200 | u | 10,00
Caixa elèctrica 746-903 Altech 450 x 300 x 94 mm | u | 137,94

### 1.3. Treball

Descripció | Unitat | Cost unitari €/h
Enginyer | h | 30,00
Oficial de primera | h | 25,00
Mà d'obra mecànic | h | 20,00
Mà d'obra electrònic | h | 20,00

### 2. PRESSUPOST PARCIAL

### 2.1. Implementació mecànica del braç

Descripció | Unitat Amid. C. unit.€/u | Cost €
Tub perfil rectangular 45 x 20 x 1,2 | mm | 240 | 0,01 | 2,40
Tallar i trepanar | h | 0,5 | 20,00 | 10,00
Tub perfil rectangular 54,76 x 18,78 x 2,04 | mm | 228,4 | 0,01 | 2,29
Tallar i trepanar | h | 0,5 | 20,00 | 10,00
Prisma 42,6 x 17,6 x 24 | u | 2 | 15,00 | 30,00
Prisma 52,8 x 16,82 x 24 | u | 2 | 15,00 | 30,00
Servo-Block Hitec 637118 | u | 2 | 35,37 | 70,74
Suport Espatlla (Peça de fabricació) | u | 1 | 30,00 | 30,00
Base Braç (Peça de fabricació) | u | 1 | 50,00 | 50,00
Base Canell (Peça de fabricació) | u | 1 | 30,00 | 30,00
DIN 7981 Cargol Auto-roscant Cap Rodó Creu M4 x 6,5 | u | 48 | 0,03 | 1,44
DIN 7985 Cargol Cap Rodó Creu M3,5 x 12 | u | 12 | 0,03 | 0,36
DIN 7985 Cargol Cap Rodó Creu M3,5 x 8 | u | 4 | 0,03 | 0,12
Realitzar el muntatge de l'estructura del braç | h | 4 | 20,00 | 80,00
Enginyer | h | 4 | 30,00 | 120,00
Oficial de primera | h | 4 | 25,00 | 100,00
| | | SUBTOTAL | 477,35 €

### 2.2. Implementació mecànica de la mà

Descripció | Quantitat C. unit.€/u | Import €
Suport Mà (Peça de fabricació) | 1 | 30,00 | 30,00
Biela Dentada Øp = 10 m=1,5 (Peça de fabricació) | 2 | 10,00 | 20,00
Biela (Peça de fabricació) | 4 | 5,00 | 20,00
Suport Goma (Peça de fabricació) | 2 | 10,00 | 20,00
Prisma Goma 10 x 40 x 40 | 2 | 5,00 | 10,00
h Tallar | 0,1 | 20,00 | 2,00
DIN 7985 Cargol Cap Rodó Creu M3,5 x 12 | 8 | 0,03 | 0,24
Barilla DIN 14021 Ø 3,5 x 40 | 4 | 0,03 | 0,12
h Tallar | 0,1 | 20,00 | 2,00
h Implementació i muntatge de la Mà | 2 | 20,00 | 40,00
h Enginyer | 2 | 30,00 | 60,00
h Oficial de primera | 2 | 25,00 | 50,00
| | SUBTOTAL | 254,36 €

### 2.3. Implementació mecànica del guant

Descripció | Unitat Amid. C. unit.€/u | Cost €
Tela | m
| 2 | 0,26 | 14,00 | 3,64
Tancament Velcro 25 x 300 | u | 4 | 30,00 | 120,00
Oficial de primera | h | 1 | 25,00 | 25,00
| | | SUBTOTAL | 148,64 €

### 2.4. Implementació electrònica del braç i mà

Descripció | Quantitat C. unit.€/u | Cost €
Robot Digital Servo RDS5160 | 1 | 25,31 | 25,31
Robot Digital Servo RDS3135 | 1 | 16,64 | 16,64
Robot Digital Servo RDS3218 | 2 | 8,23 | 16,46
Digital Servo HS-785HB | 2 | 34,00 | 68,00
Cable DuPont Mascle-Mascle | 40 | 0,08 | 3,20
Cable DuPont Mascle-Femella | 80 | 0,08 | 6,40
DC-DC XH-M401 | 3 | 6,00 | 18,00
h Connectar i soldar els diferents components | 2 | 20,00 | 40,00
h Enginyer | 2 | 30,00 | 60,00
h Oficial de primera | 2 | 25,00 | 50,00
| | SUBTOTAL | 304,01 €

### 2.5. Implementació electrònica del guant i processador

Descripció | Quantitat C. unit.€/u | Cost €
Arduino Uno | 1 | 20,00 | 20,00
Giroscopi MPU-6050 | 4 | 4,00 | 16,00
Multiplexor TCA9548A | 1 | 5,00 | 5,00
Cable DuPont Mascle-Mascle | 40 | 0,08 | 3,20
Cable DuPont Mascle-Femella | 80 | 0,08 | 6,40
Transformador DC-DC XH-M401 | 1 | 6,00 | 6,00
Font GHB 12V ESP127 | 1 | 50,00 | 50,00
Polsador B3F | 1 | 0,245 | 0,245
Placa fibra doble cara 80x120 mm | 1 | 4,25 | 4,25
Nucli de ferrita Vk200 | 1 | 10,00 | 10,00
Caixa eléctrica 746-903 Altech 450 mm x 300 mm x 94 mm | 1 | 137,94 | 137,94
Connectar i soldar dels diferents components | 2 | 20,00 | 40,00
Enginyer | 2 | 20,00 | 60,00
Oficial de primera | 2 | 20,00 | 50,00
| | SUBTOTAL | 409,04 €

### 2.6. Implementació programa

Descripció | Unitat Amid. C. unit.€/u | Cost €
Enginyer | h | 20 | 30,00 | 600,00€
| | | SUBTOTAL | 600,00 €

### 2.7. Posada en funcionament

Descripció | Unitat Amid. C. unit.€/u | Cost €
Enginyer | h | 4 | 30,00 | 600,00€
Oficial de primera | h | 4 | 25,00 | 100,00€
| | | SUBTOTAL | 600,00 €

### 3. PRESSUPOST TOTAL

Descripció | Import
Implementació mecànica del braç | 477,35 €
Implementació mecànica de la mà | 254,36 €
Implementació mecànica del guant | 148,64 €
Implementació electrònica del braç i mà | 304,01 €
Implementació electrònica del guant i processador | 409,04 €
Implementació programa | 600,00 €
Posada en funcionament | 220,00 €
BASE IMPOSABLE | 2.213,40 €
21% IVA | 464,82 €
TOTAL | 2.678,22 €

Josep Rueda Collell

Graduat en Enginyeria Mecànica.

Girona, 6 de juny de 2019

# ANNEX AL PRESSUPOST

A.1. Cost del projecte

Aquest annex resumeix el cost de redacció del projecte.

Descripció | Hores | Cost (€/h) | Import
Projectista | 400 | 10,00 4.000,00 €
| | TOTAL | 4.000,00 €

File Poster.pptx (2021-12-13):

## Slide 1

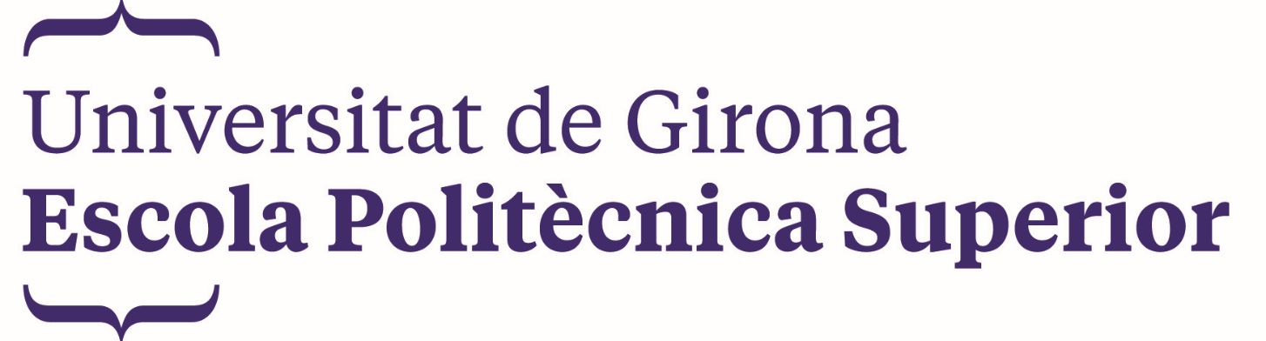
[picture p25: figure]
EPS transparent qualitat

Josep Rueda Collell Professor/a tutor/a: Dr. Narcís Gascons
Grau en Enginyeria Mecànica Enginyeria Mecànica i de la Construcció Industrial

Disseny d’un braç robòtic controlat per un guant electrònic

Hem dissenyat un braç robòtic amb una estructura similar a la d’un braç humà, destinat a ser utilitzat en un laboratori químic. Aquest ha de ser capaç de moure i decantar provetes o altres recipients de caràcter similar. Per fer això ha de ser capaç de copiar els moviments d’un guant, que duria un operari al voltant del braç, la qual cosa faria el control fàcil i intuïtiu. També incorpora un sistema de control de posició per evitar col·lisions.


Introducció
El projecte es basa en dissenyar un braç robòtic, capaç de copiar els moviments d’un guant, el qual un operari duria al voltant del braç.
El braç està pensat per treballar dins d’una campana d‘un laboratori químic i com a tal, aquest ha de ser capaç de moure i decantar provetes o altres recipients de caràcter similar.
Per tal de fer el control fàcil i intuïtiu, tindrà una estructura similar a la d’un braç humà.

Algoritme
De forma periòdica, prenem mesures dels sensors que ens determinen la posició del braç de l’operari.
Per normativa i per seguretat, el braç no pot tocar les parets de la campana, per tant, previ a copiar la seva posició, comprovem si tal posició resultaria en una col·lisió amb les parets.
En acabat, calculem una posició vàlida pel braç robòtic i aquest la implementa. D’aquesta forma podem fer que l’operari mogui el braç lliurement sense preocupar-se que aquest xoqui de cap manera.


Funcionament del guant
El guant duu quatre sensors de tipus giroscopi que llegeixen el valor del gir de les articulacions de l’operari.
Aquests utilitzen l’eix de la gravetat per a corregir l’acumulació de l’error al llarg del temps, aconseguint així lectures fiables en tot moment.


Estructura del braç
El conjunt del braç rota entorn un eix perpendicular al terra. Aquest conjunt està format per una espatlla, un colze i un canell que dibuixen un pla de moviments. Finalment, al canell hi ha una pinça la qual pot rotar sobre un eix per poder decantar les provetes, tanmateix aquest eix s’ha de mantenir sempre paral·lel al terra.


25a. Edició Premis Patronat Politècnica. Projectes Final de Carrera

Model matemàtic
Tot el braç ha estat modelat matemàticament. Això ens permet aplicar cinemàtica directa i cinemàtica inversa. Això significa que si li apliquem al braç uns angles determinats per a cada articulació, podem determinar la posició exacta de la pinça, i viceversa, que per a una posició concreta de la pinça podem saber la posició angular de cadascuna de les articulacions.
Això facilita molt la implementació directa de les lectures dels sensors del guant.

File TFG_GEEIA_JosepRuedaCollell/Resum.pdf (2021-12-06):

# Treball final de grau

Estudi: Grau en Enginyeria Electrònica | Industrial i
. | Automàtica

## Títol:

# Disseny d’un braç robòtic controlat per un guant electrònic

## Document: Resum

## Alumne: Josep Rueda Collell

## Tutor: Miquel Rustullet Reñe Departament: Enginyeria Elèctrica, Electrònica i Automàtica Àrea: Enginyeria de Sistemes i Automàtica

## Convocatòria: Juny 2019

Disseny d’un braç robòtic controlat per un guant electrònic | Resum

INDEX:

Disseny d’un braç robòtic controlat per un guant electrònic | Memòria i annexos

### 1. Introducció:

L’institut de Duve és un institut a Bèlgica enfocat a la recerca genètica i biotecnològica.

Per a la realització de les conseqüents investigacions, els seus laboratoris, estan equipats

amb un seguit d’instal·lacions especialitzades per a la realització de les tasques

específiques.

El Sr. Marcel McCullough, científic dels laboratoris del Duve Institute ens explica que,

habitualment, en aquest àmbit de recerca, s’han de fer processos en condicions

potencialment perilloses, ja sigui perquè treballen amb elements a temperatures massa

fredes per ser aptes pel contacte humà o amb substàncies tòxiques o corrosives. Dur la

conseqüent vestidura protectora, pot dificultar i, fins i tot, impossibilitar la realització de

certes tasques.

L’objecte del projecte és dissenyar un braç robòtic, capaç de moure provetes i tubs d’assaig,

copiant els moviments d’un guant que duria un operari al voltant del braç. Juntament amb el

disseny del guant i el del braç adjuntarem un programa en codi Arduino capaç de garantir-

ne el control.

El projecte inclourà el disseny mecànic acord amb les necessitats del client així com un

estudi per justificar les dimensions escollides. També inclou el dimensionament i tria del

components electrònics i hardware, així com els detalls per a la correcta connexió entre ells

i finalment detalls i instruccions per a la correcta implementació del codi, així com un annex

amb simulacions utilitzant l’eina “Robotix Toolbox” utilitzada pel correcte desenvolupament

del projecte.

El braç ha de cabre dins una campana de laboratori de 1400 mm d’ample, 1100 mm d’alt i

800 mm de profunditat l’eix de la mà sempre ha d’anar paral·lel al terra. Tanmateix, degut a

la normativa dels laboratoris, s’haurà d’evitar que ni el braç del robot entri en contacte amb

les parets de la campana.

### 2. Conjunt braç

Hem estudiat diferents distribucions pel braç dins de la campana i diferents combinacions de

longituds pels diferents components d’aquest. Després de varies combinacions, hem escollit

la que ens ha semblat més òptima a fi de poder aprofitar millor les dimensions de la

campana, l’espai de treball i la facilitat d’us per part de l’operari.

Per realitzar el disseny del braç hem tingut en compte les dimensions anteriorment

especificades, a fi de poder realitzar la unió de les peces de forma eficaç i poder realitzar la

tasca de poder moure i decantar provetes. Cal recordar que pel dimensionament del braç,

s’ha tingut en compte que només es requerirà desplaçar i decant provetes, per tant era

redundant que el braç pogués fer tots els moviments d’un braç humà. Dit això se li han

eliminat certs moviments i graus de llibertat, fent la comparativa amb un braç humà.

El resultat ha estat un braç de 5 graus de llibertat més el control de la obertura de la pinça.

Tanmateix, el requeriment que la mà de la pinça s’havia de mantenir sempre paral·lela al pla

del terra, fa que virtualment sigui un robot amb 4 graus de llibertat més el control de

l’obertura de la pinça. Per a cada articulació del braç hem escollit el pertinent servomotor a fi

que puguin sostenir les provetes i el propi pes del braç.

Seguidament hem escollit els giroscopis que utilitzarem per sonoritzar el braç i hem explicat

on els situaríem i com els connectarem a la unitat de control. Llegint la posició angular dels

giroscopis, podem sevir la inclinació del braç de l’operari i d’aquesta manera, el robot és

capaç de reproduir el mateixos moviments que fa l’operari amb el braç. Una unitat Arduino

Uno s’encarrega de processar les dades pertinents llegides des dels sensors, i transmetre

els conseqüents valors als servomotors.

El projecte també inclou el disseny de la instal·lació elèctrica i electrònica a fi que tots els

dispositius els arribi el voltatge adient per poder suplir les seves necessitats energètiques.

### 3. Descripció del programa

El processador, adquireix la lectura dels angles de cada sensor de forma continuada.

Cada cop que s’executa el programa, pren els valors dels angles prèviament adquirits, i

calcula la posició X, Y i Z mitjançant cinemàtica directe de la punta de la pinça.

Seguidament, el programa comprova si aquesta posició X de la pinça és dins de la dimensió

X de la campana. Si és a dins, transmet els valor dels angles al seus respectius

servomotors, si es a fora, assignem al valor X de la posició de la pinça, el mateix valor X del

límit de la campana i li fem calcular un altre cop, mitjançant cinemàtica inversa, els valors

del angles de cada articulació. Finalment assignem els nous angles calculats al seu

respectiu servomotor.

D’aquesta manera podem complir amb el requisit que no es podia tocar el vidre de la

campana ni amb la pinça ni amb una proveta.

Finalment, desprès d’haver enviat les consignes d’angle als servomotors, es comprova si el

polsador ha estat premut o no a fi de controlar la obertura i el tancament de la pinça.

Seguidament el programa torna a iniciar un cicle.

### 4. Conclusions

Hem implementat un braç està pensat per treballar dins d’una campana de químics, a fi de

realitzar tasques en unes condicions on un braç humà no podria fer-ho correctament degut

al risc a les lesions i perjudicis contra entitats humanes.

El disseny del braç no permet que la pinça topi contra el vidre de les parets de la campana

on treballa, tal i com s’havia especificat als requeriments. Tanmateix si que podria topar

contra el terra, ja que no s’ha tingut en compte cap limitació respecte aquest.

Quan l’operari obliga al robot a fer un moviment, el qual faria xocar el braç contra el vidre de

la campana, el programa, tal i com s’havia especificat als requeriments s’ha d’abstenir de

topar-hi. Quan es dona aquesta situació, el braç passa per un seguit de càlculs amb base

trigonomètrica que li permeten emular moviments semblants als de l’operari en quant al

desplaçament lineal de la pinça, però divergents en quant als valors absoluts dels angles de

les articulacions del guant.

El braç te limitacions respecte als angles de treball. Les equacions amb base trigonomètrica

que el nostre sistema duu integrades, poden calcular varis valors diferents pels angles per a

certes posicions del braç. D’aquí que puguin sorgir interpretacions errònies de la posició real

del braç. Dit això, l’operari s’ha d’abstenir a que la espatlla, tingui una inclinació superior a

un pla paral·lel al terra. Recordem que aquesta limitació només sorgeix quan hi ha risc que

el braç topi amb les parets de la campana.

S’ha de tenir en compte que el funcionament del sistema és reconfigurable, podent ampliar

les funcions d’aquest inversor i afegint o modificant les prestacions.

Josep Rueda Collell

Graduat en enginyeria Electrònica Industrial i Automàtica.

Girona, 6 de juny de 2019

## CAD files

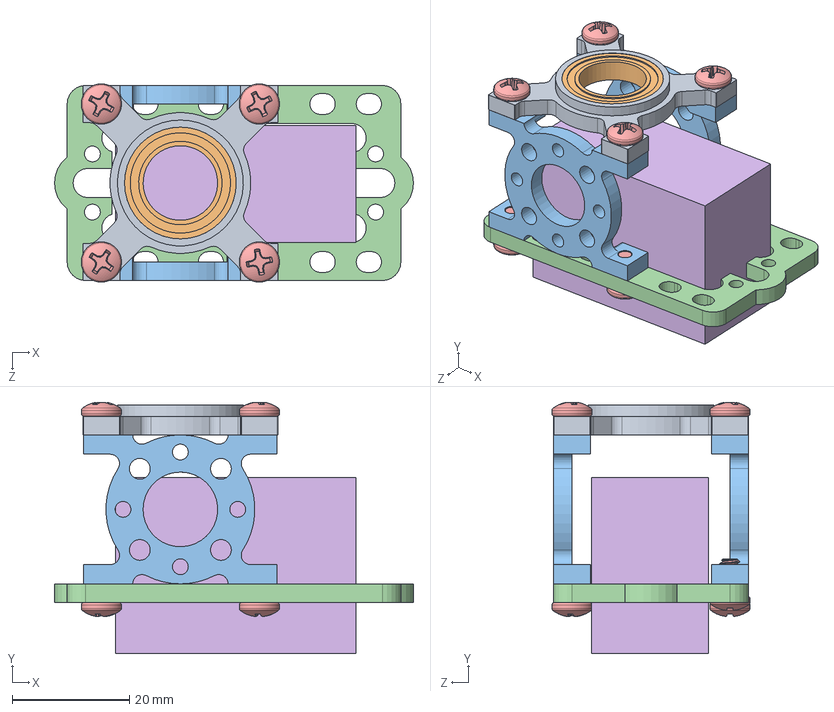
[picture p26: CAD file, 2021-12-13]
SolidWorks/LOAD-BEARING-SERVO.SLDASM
61.2 x 42.8 x 33.8 mm
.5 x .75 non flanged bearing
90272A144 x 8
servo

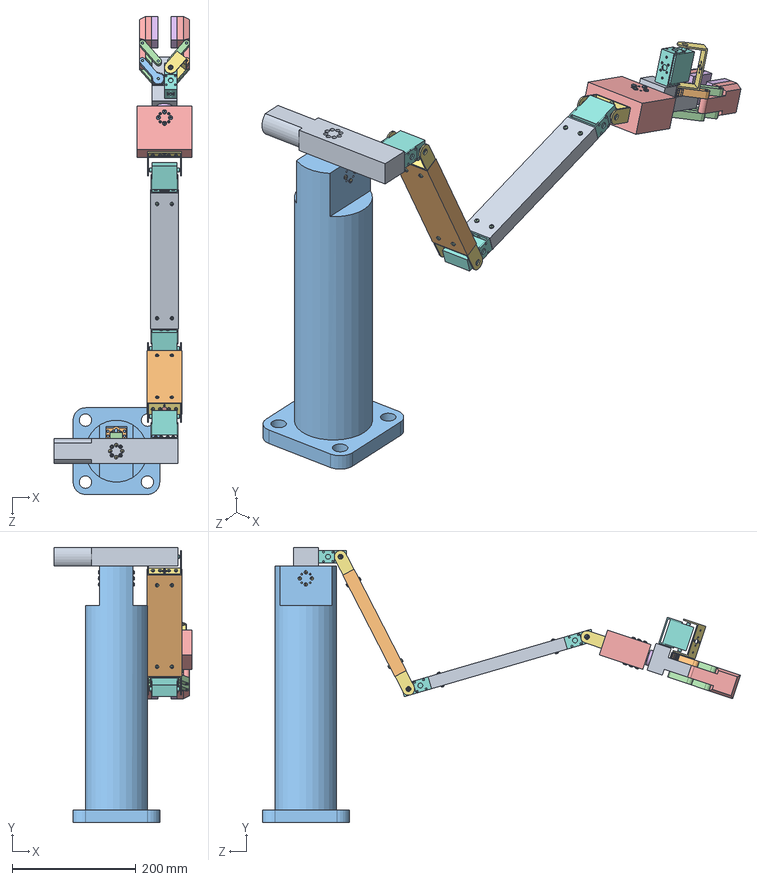
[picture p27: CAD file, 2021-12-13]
SolidWorks/Ensamblaje1_bona.SLDASM
221.9 x 444.0 x 771.4 mm
base
gear1
gear2
eix x 6
pinça x 2
goma x 2
.5 x .75 non flanged bearing x 2
90272A144 x 28
servo x 2
Pieza12
Pieza5 x 4
Pieza6 x 4
avantbraç
braç
Pieza13
sheet metal screws_din x 48
dau1 x 2
dau2 x 2
pan head cross recess screw_din x 12
Barilla x 8
Pieza4_bona

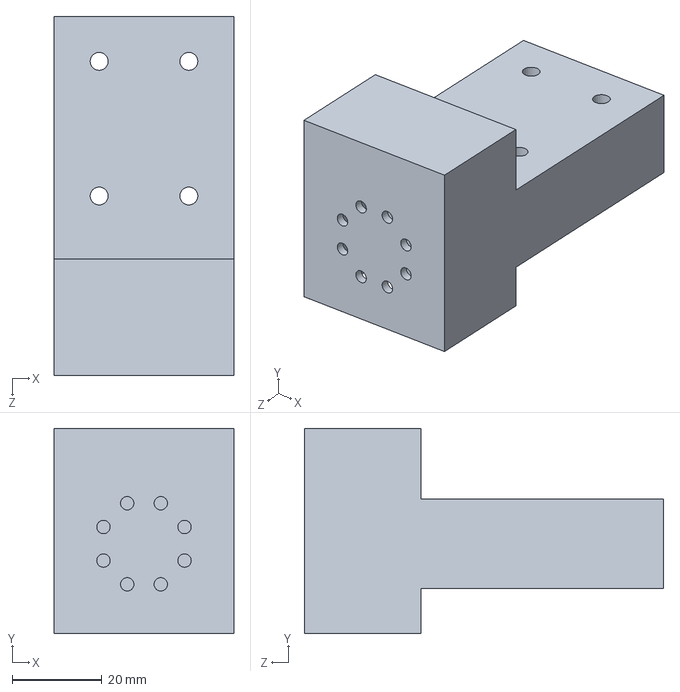
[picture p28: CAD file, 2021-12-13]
SolidWorks/base.SLDPRT
40.0 x 45.7 x 80.0 mm

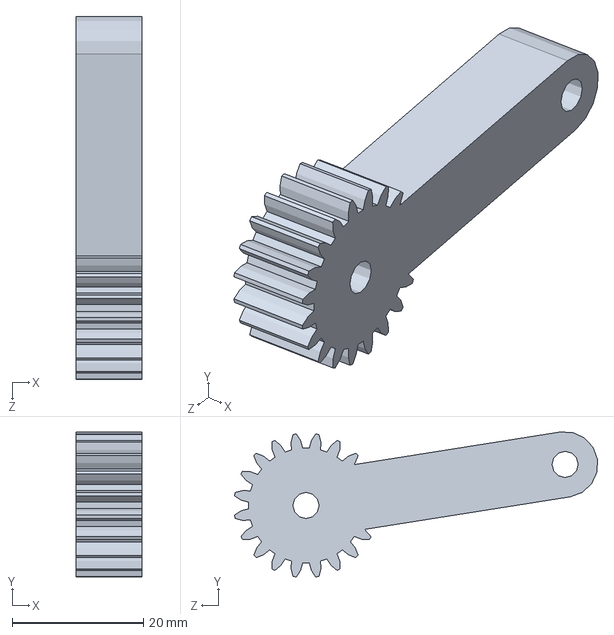
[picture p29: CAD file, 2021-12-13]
SolidWorks/gear2.sldprt
10.0 x 22.1 x 55.3 mm

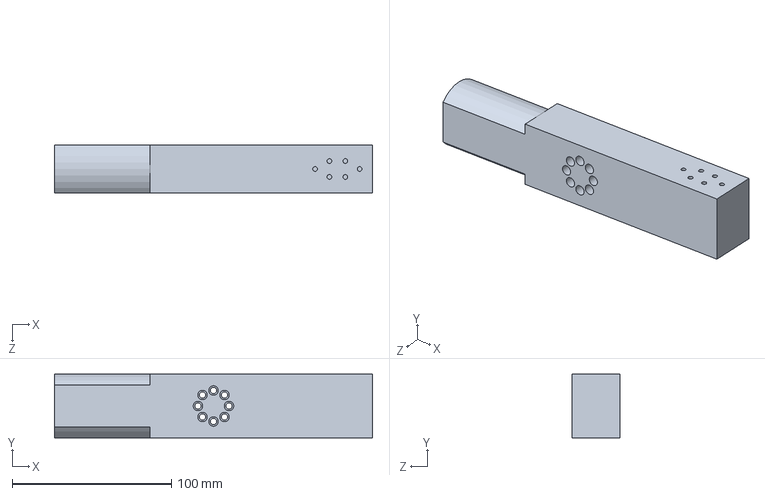
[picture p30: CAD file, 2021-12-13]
SolidWorks/Pieza4_bona.SLDPRT
200.0 x 40.0 x 30.0 mm

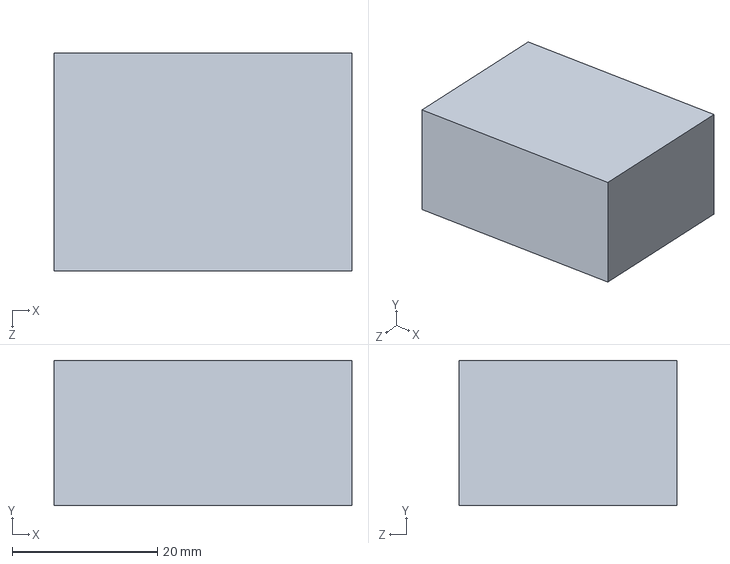
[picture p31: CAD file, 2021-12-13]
SolidWorks/servo.SLDPRT
41.0 x 20.0 x 30.0 mm

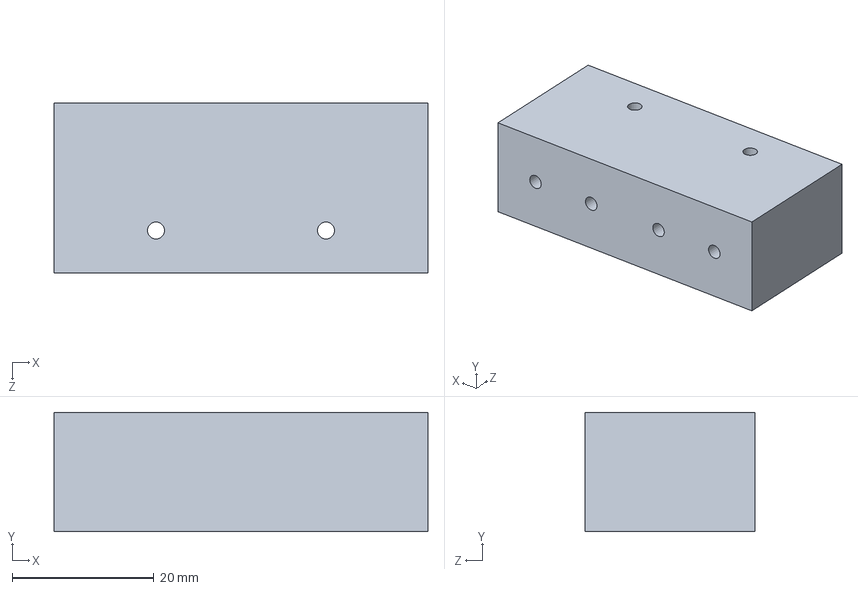
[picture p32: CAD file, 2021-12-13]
SolidWorks/dau1.SLDPRT
52.8 x 16.8 x 24.0 mm

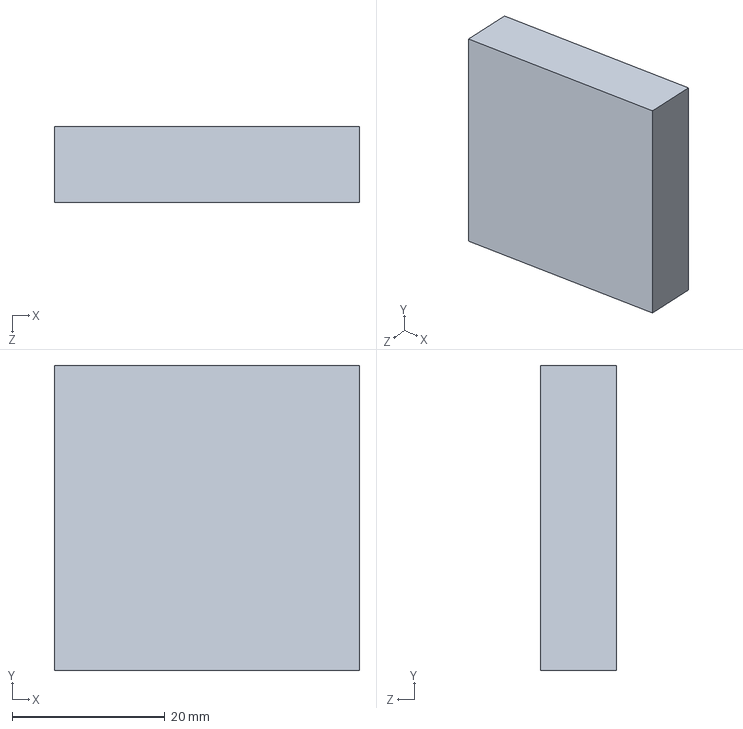
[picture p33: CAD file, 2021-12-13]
SolidWorks/goma.SLDPRT
40.0 x 40.0 x 10.0 mm

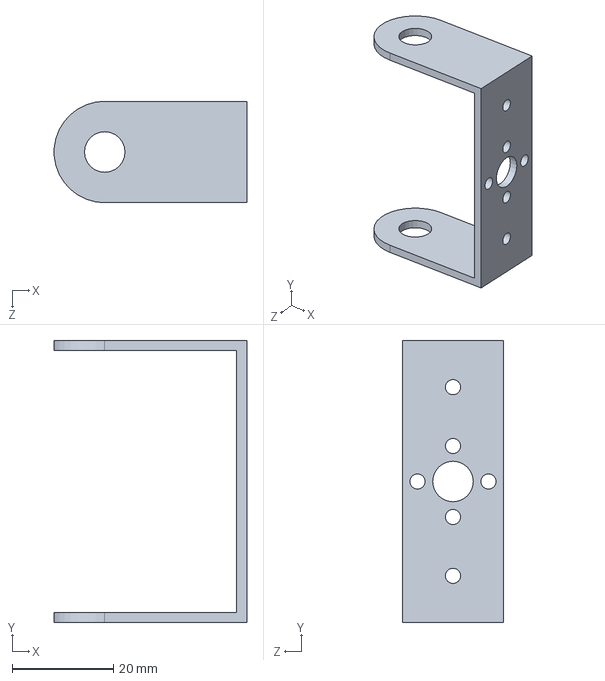
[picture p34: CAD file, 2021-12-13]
SolidWorks/Pieza5.SLDPRT
38.0 x 55.6 x 20.0 mm

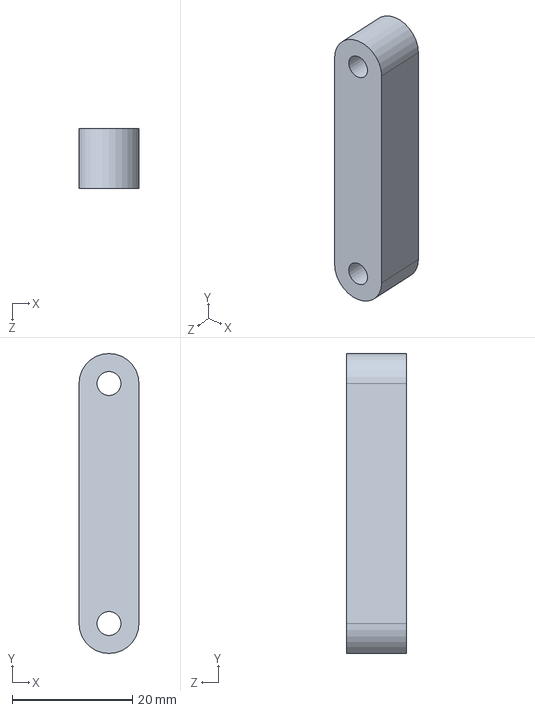
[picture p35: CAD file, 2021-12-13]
SolidWorks/eix.SLDPRT
10.0 x 50.0 x 10.0 mm

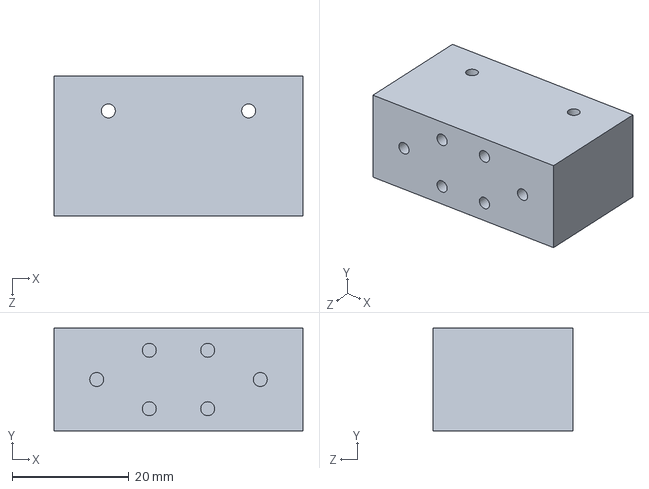
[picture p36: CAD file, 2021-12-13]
SolidWorks/dau2.SLDPRT
42.6 x 17.6 x 24.0 mm

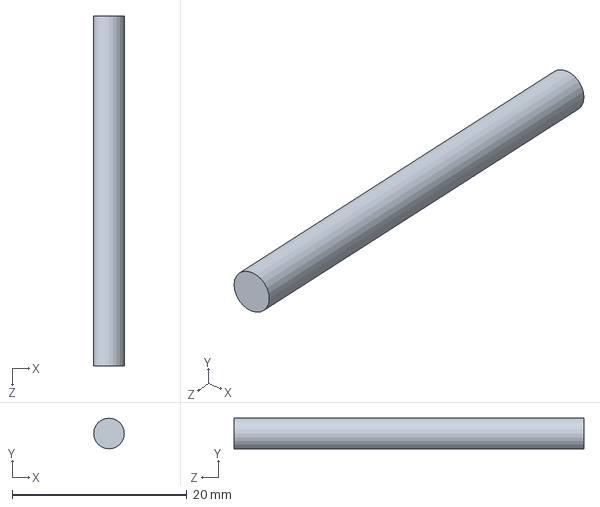
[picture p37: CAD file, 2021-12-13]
SolidWorks/Barilla.SLDPRT
3.50 x 3.50 x 40.0 mm

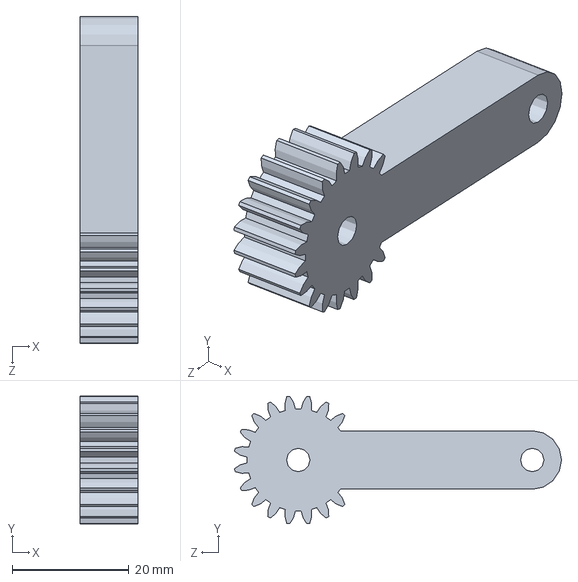
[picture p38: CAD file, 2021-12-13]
SolidWorks/gear1.sldprt
10.0 x 21.8 x 55.9 mm

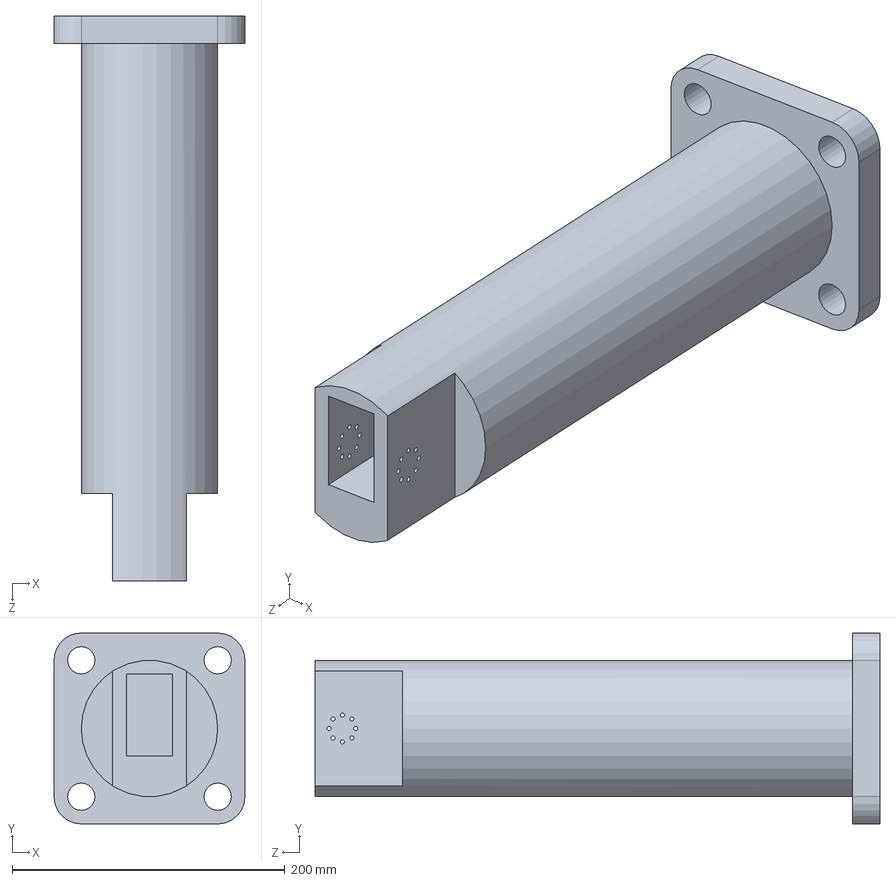
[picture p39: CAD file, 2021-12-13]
SolidWorks/Pieza13.SLDPRT
140.0 x 140.0 x 414.0 mm

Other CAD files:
SolidWorks/braç.SLDPRT
SolidWorks/Pieza6.SLDPRT
SolidWorks/.5 x .75 non flanged bearing.sldprt
SolidWorks/pinça.SLDPRT
SolidWorks/525123.SLDPRT
SolidWorks/535118 assembly1.SLDASM
SolidWorks/535118.sldprt
SolidWorks/545420.SLDPRT
SolidWorks/575112.SLDPRT
SolidWorks/90272A144.SLDPRT
SolidWorks/Pieza12.SLDPRT
SolidWorks/avantbraç.SLDPRT

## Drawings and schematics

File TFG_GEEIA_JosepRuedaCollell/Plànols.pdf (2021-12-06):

## Treball final de grau

Estudi: Grau en Enginyeria Electrònica Industrial i
. | Automàtica

Títol:

## Disseny d’un braç robòtic controlat per un guant electrònic

Document 2: Plànols

Alumne: Josep Rueda Collell

Tutor: Miquel Rustullet Reñe
Departament: Enginyeria Elèctrica, Electrònica i Automàtica Àrea: Enginyeria de Sistemes i Automàtica

Convocatòria: Juny/2019

Disseny d’un braç robòtic controlat per guant elec | Plànols

INDEX

1. ESQUEMA ELECTRÒNIC
2. DISSENY PLACA
3. DISTRIBUCIÓ CAIXA

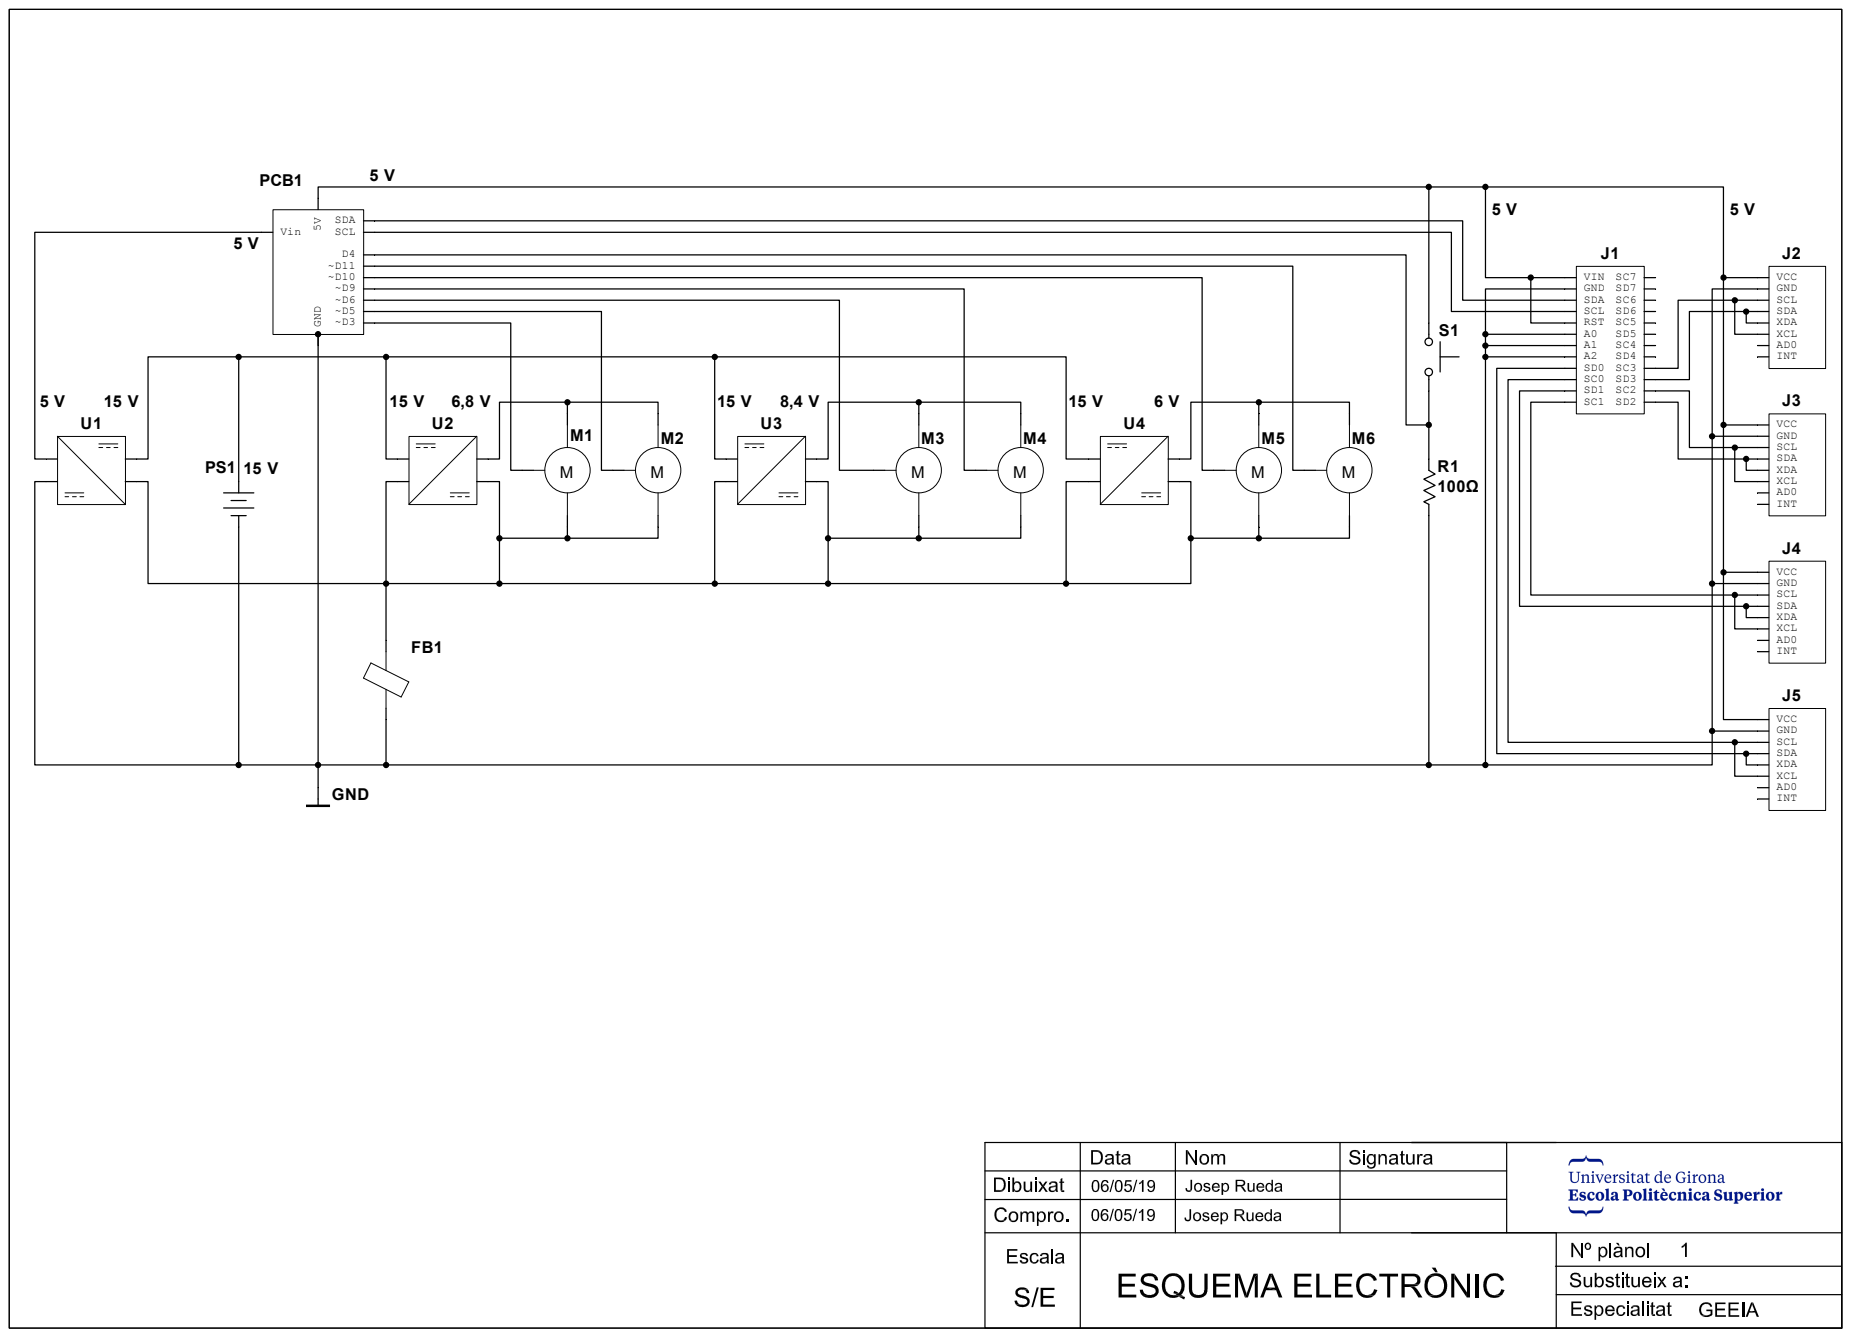
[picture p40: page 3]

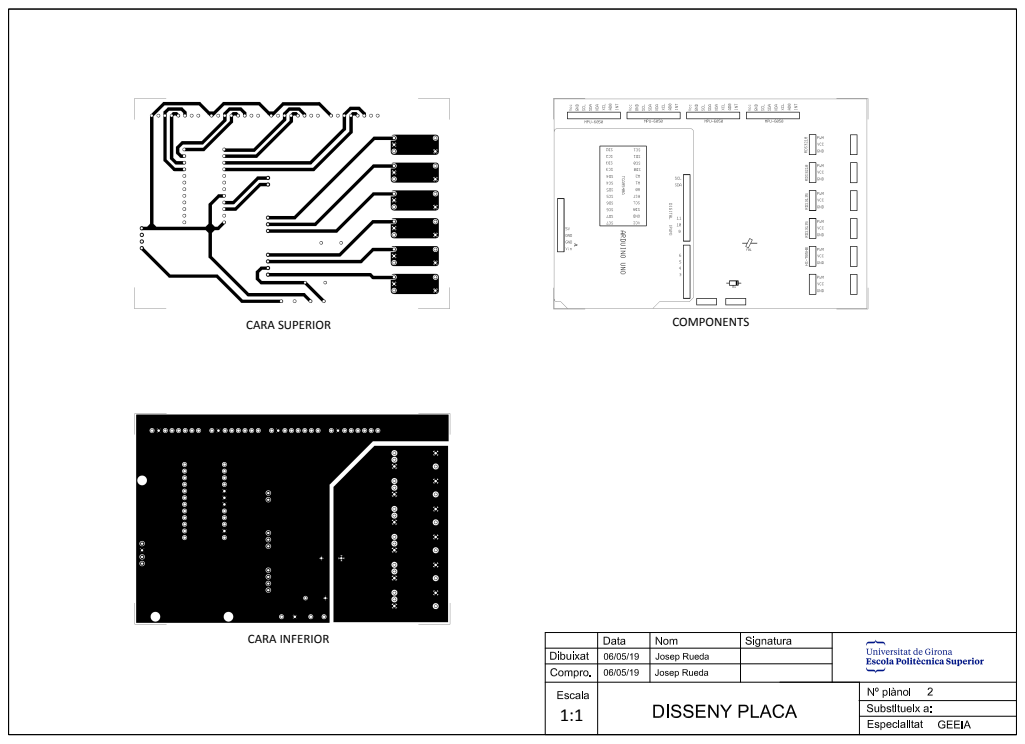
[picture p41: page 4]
CARA INFERIOR; CARA SUPERIOR; COMPONENTS

~ 230 V

### XH-M401

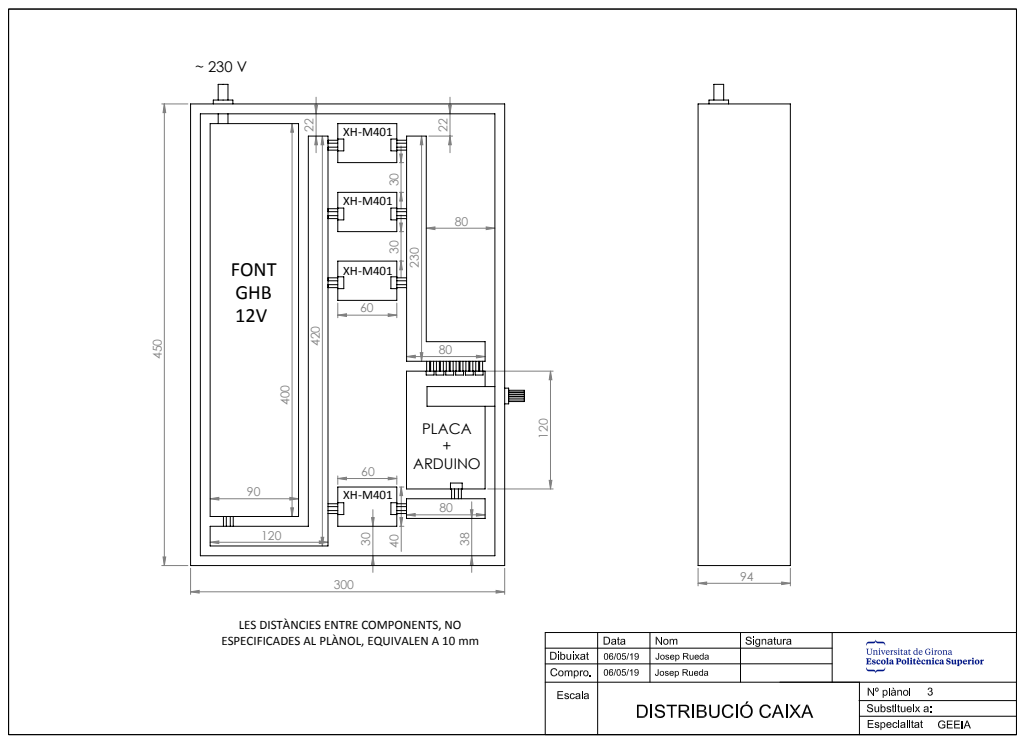
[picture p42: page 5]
PLACA + ARDUINO; FONT GHB 12V

LES DISTÀNCIES ENTRE COMPONENTS, NO
ESPECIFICADES AL PLÀNOL, EQUIVALEN A 10 mm

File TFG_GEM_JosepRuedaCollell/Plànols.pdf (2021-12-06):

## Treball final de grau

Estudi: Grau en Enginyeria Mecànica

Títol:

## Disseny d’un braç robòtic controlat per un guant electrònic

Document 2: Plànols

Alumne: Josep Rueda Collell

Tutor: Narcís Gascons Clarió
Departament: Enginyeria Mecànica i de la Construcció Industrial Àrea: Enginyeria Mecànica

Convocatòria: Juny/2019

Disseny d’un braç robòtic controlat per un guant electrònic | Plànols

ÍNDEX:
CONJUNT BRAÇ | PLÀNOL 1
SUBCONJUNT MÀ | PLÀNOL 2
SUPORT GOMA | PLÀNOL 3
BIELA I BIELA DENTADA | PLÀNOL 4
SUPORT MÀ | PLÀNOL 5
BASE BRAÇ | PLÀNOL 6
SUPORT ESPATLLA | PLÀNOL 7
SUBCONJUNT ESPATLLA-ESQUENA | PLÀNOL 8
BASE CANELL | PLÀNOL 9
SUBCONJUNT AVANTBRAÇ - SERVO - BASE CANELL | PLÀNOL 10
SUBCONJUNT BRAÇ - SERVO - AVANTBRAÇ | PLÀNOL 11
SUBCONJUNT ESPATLLA - SERVO - BRAÇ | PLÀNOL 12
DISTRIBUCIÓ FORATS TUBS I PRISMES | PLÀNOL 13
ESQUEMA ELECTRÒNIC | PLÀNOL 14
DISSENY PLACA | PLÀNOL 15
DISTRIBUCIÓ CAIXA | PLÀNOL 16

16

12

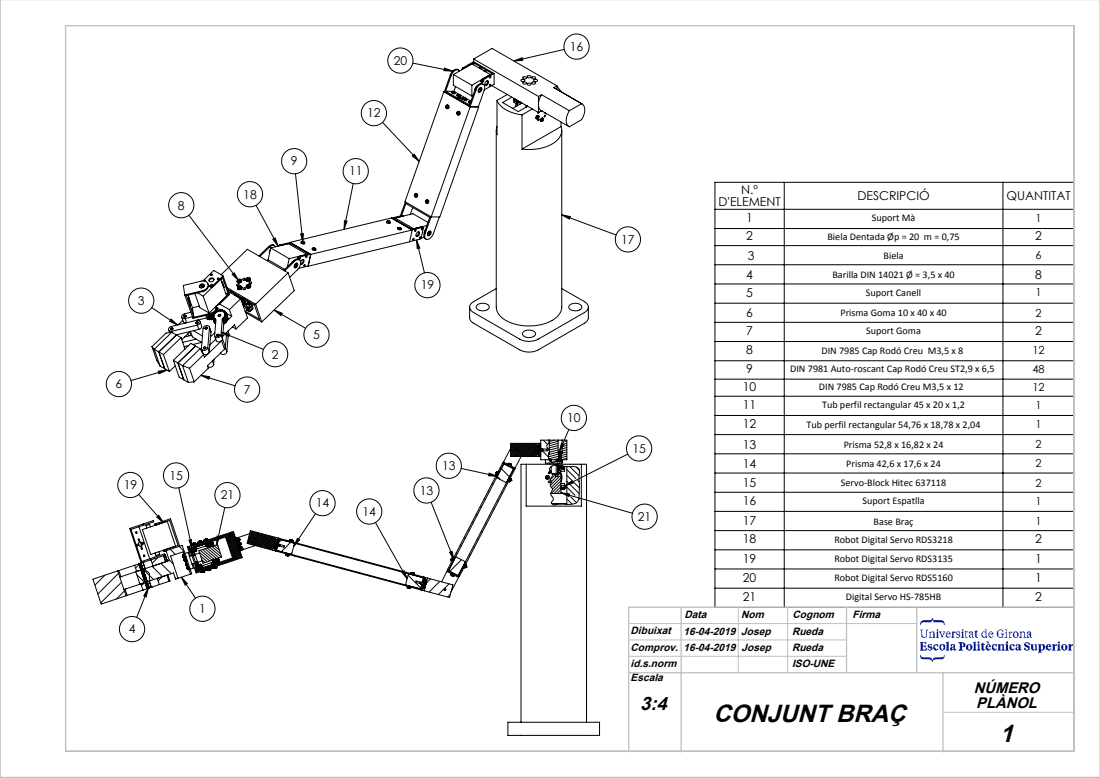
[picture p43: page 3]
D'ELEMENT; DESCRIPCIÓ; QUANTITAT 1; Suport Mà; Biela Dentada Øp = 20 m = 0,75

3 | Biela | 6
4 | Barilla DIN 14021 Ø = 3,5 x 40 | 8
5 | Suport Canell | 1
6 | Prisma Goma 10 x 40 x 40 | 2
7 | Suport Goma | 2
8 | DIN 7981 Auto-roscant Cap Rodó Creu ST2,9 x 6,5 DIN 7985 Cap Rodó Creu M3,5 x 8 | 12 9 48

10 | DIN 7985 Cap Rodó Creu M3,5 x 12 | 12
11 | Tub perfil rectangular 45 x 20 x 1,2 | 1
12 | Tub perfil rectangular 54,76 x 18,78 x 2,04 | 1
13 | Prisma 52,8 x 16,82 x 24 | 2
14 | Prisma 42,6 x 17,6 x 24 | 2
15 | Servo-Block Hitec 637118 | 2
16 | Suport Espatlla | 1
17 | Base Braç | 1
18 | Robot Digital Servo RDS3218 | 2
19 | Robot Digital Servo RDS3135 | 1
20 | Robot Digital Servo RDS5160 | 1
21 | Digital Servo HS-785HB | 2

Data | Nom | Cognom | Firma
Escala 3:4 | CONJUNT BRAÇ | NÚMERO PLÀNOL 1

Dibuixat | 16-04-2019 | Josep | Rueda
Comprov. | 16-04-2019 Josep | | Rueda
id.s.norm | | | ISO-UNE

12

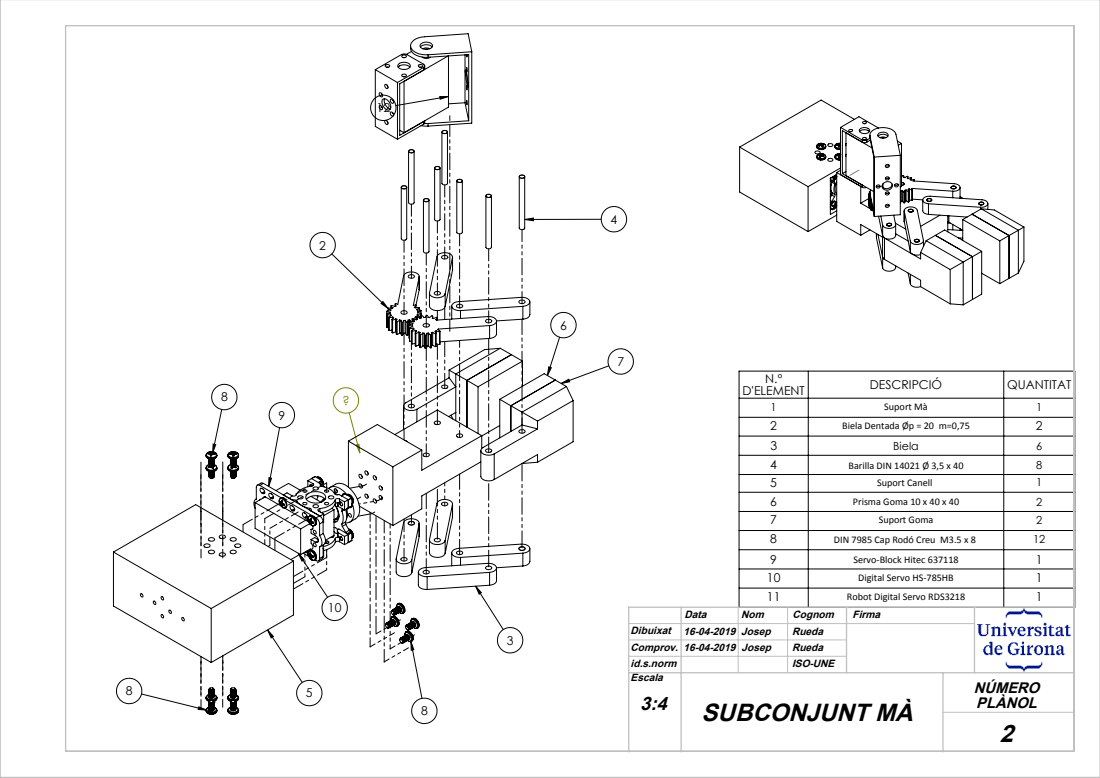
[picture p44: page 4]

N.º D'ELEMENT | DESCRIPCIÓ | QUANTITAT

1 | Suport Mà | 1
2 | Biela Dentada Øp = 20 m=0,75 | 2
3 | Biela | 6
4 | Barilla DIN 14021 Ø 3,5 x 40 | 8
5 | Suport Canell | 1
6 | Prisma Goma 10 x 40 x 40 | 2
7 | Suport Goma | 2
8 | DIN 7985 Cap Rodó Creu M3.5 x 8 | 12
9 | Servo-Block Hitec 637118 | 1
10 | Digital Servo HS-785HB | 1
11 | Robot Digital Servo RDS3218 | 1

Data | Nom | Cognom | Firma
Escala 3:4 | SUBCONJUNT MÀ | NÚMERO PLÀNOL

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

4
30

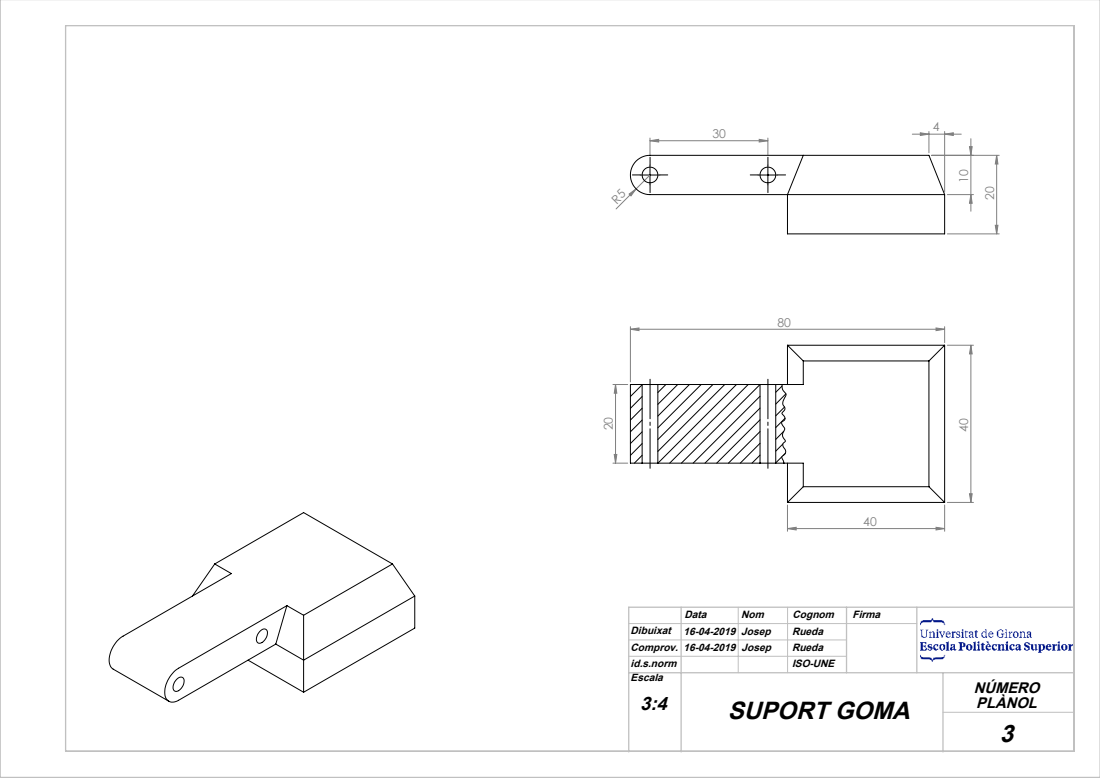
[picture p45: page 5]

Data | Nom | Cognom | Firma
Escala 3:4 | SUPORT GOMA | NÚMERO PLÀNOL

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

p = 20
m = 0,75

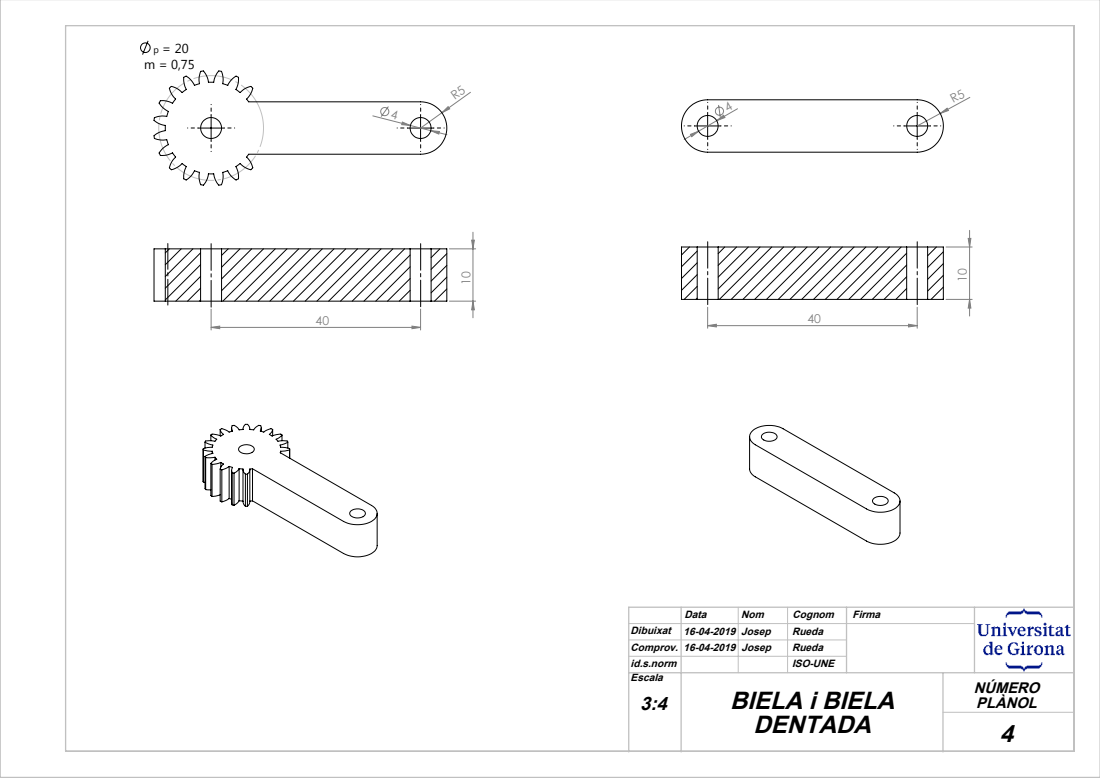
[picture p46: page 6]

Data | Nom | Cognom | Firma
Escala 3:4 | BIELA i BIELA DENTADA | NÚMERO PLÀNOL

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

20 | 4

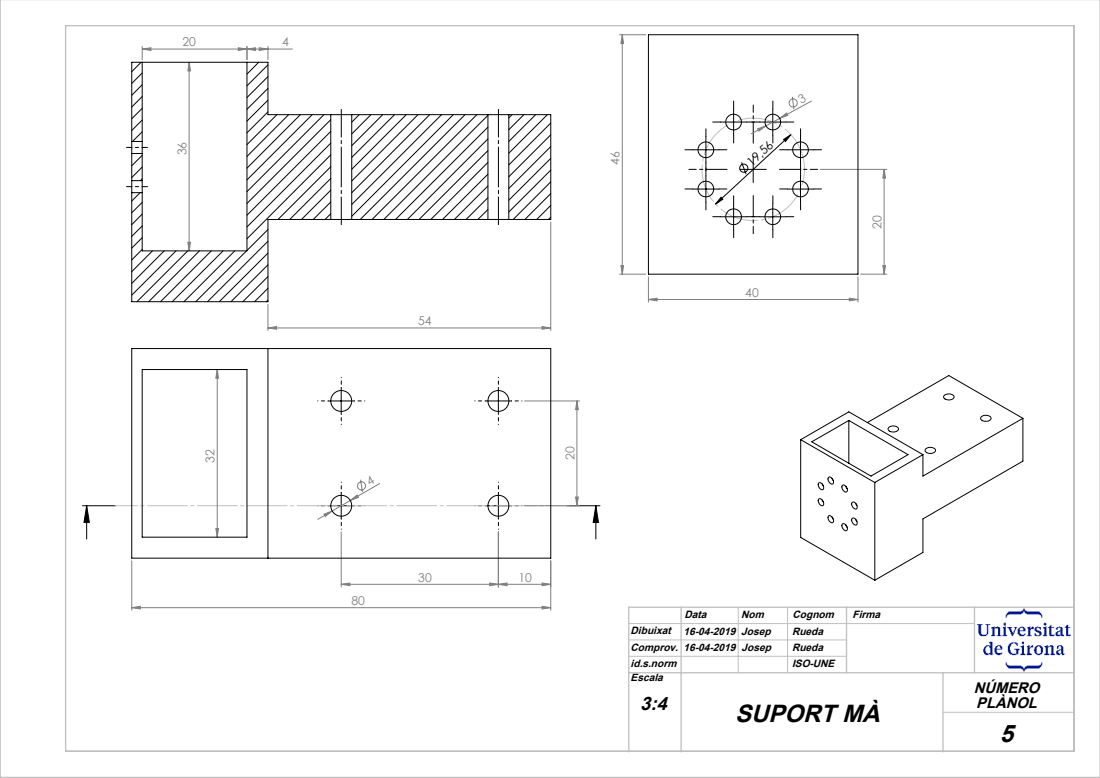
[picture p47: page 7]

Data | Nom | Cognom | Firma
Escala 3:4 | SUPORT MÀ | NÚMERO PLÀNOL

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

100 R20

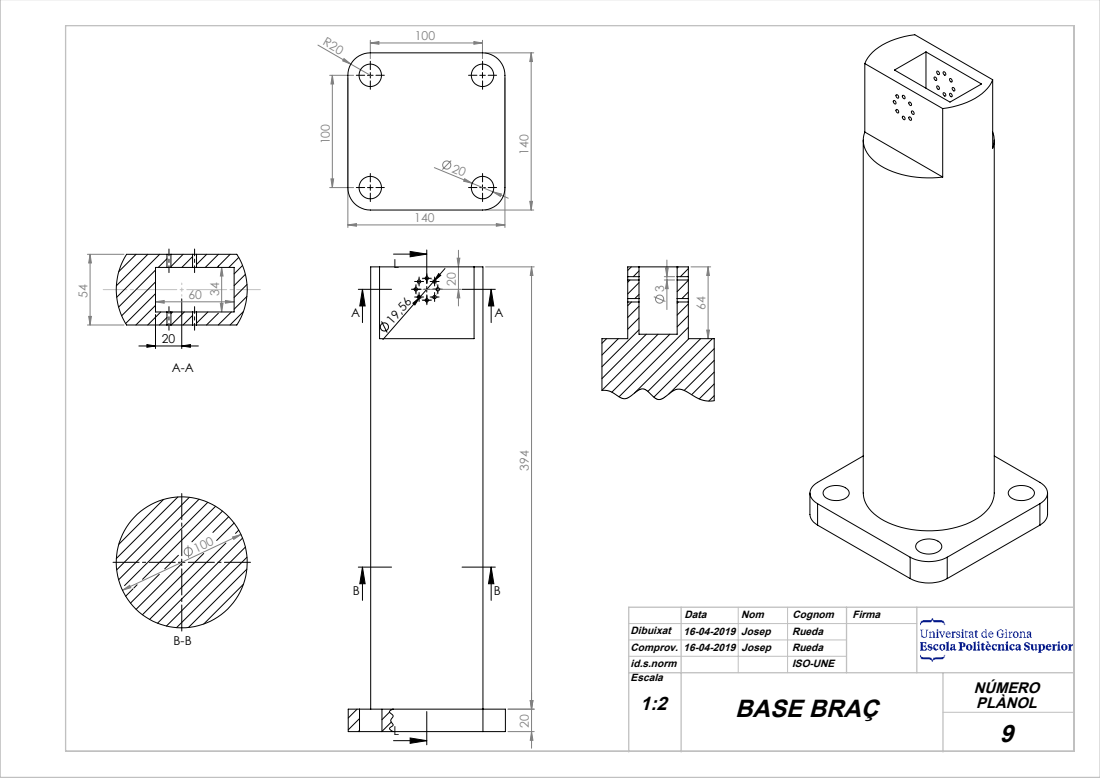
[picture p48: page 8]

Data | Nom | Cognom | Firma
Escala 1:2 | BASE BRAÇ | NÚMERO PLÀNOL

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

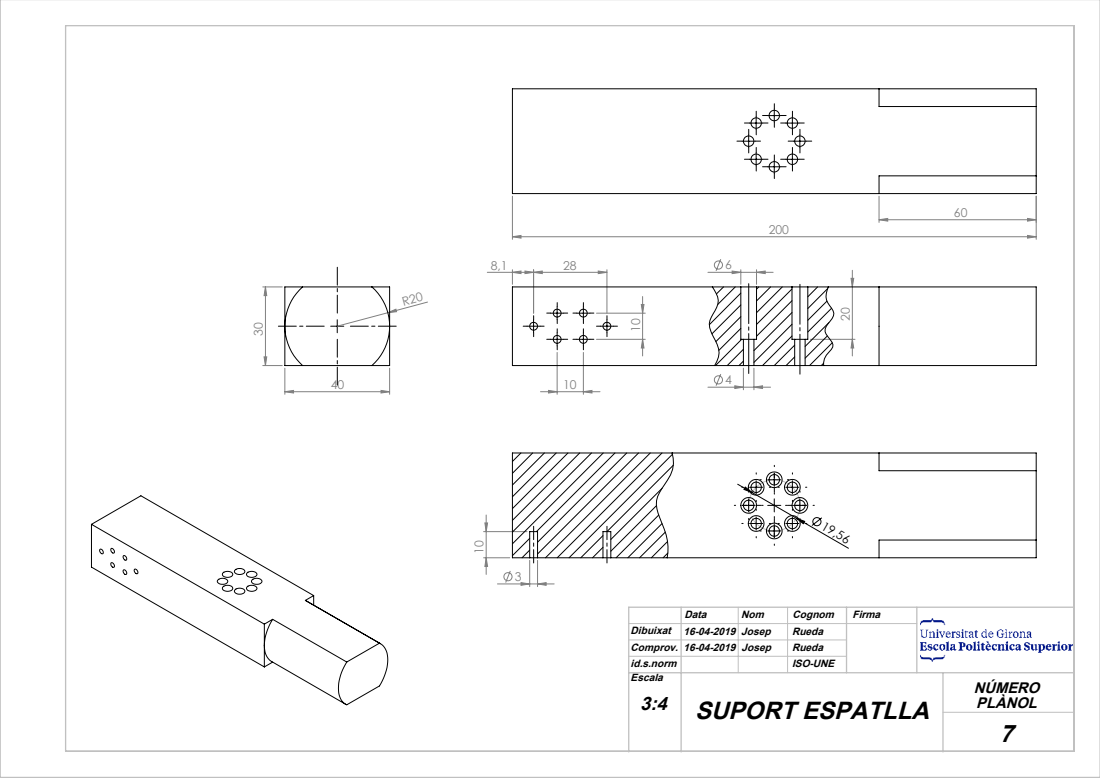
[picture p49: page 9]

Data | Nom | Cognom | Firma
Escala 3:4 | SUPORT ESPATLLA | NÚMERO PLÀNOL

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

3

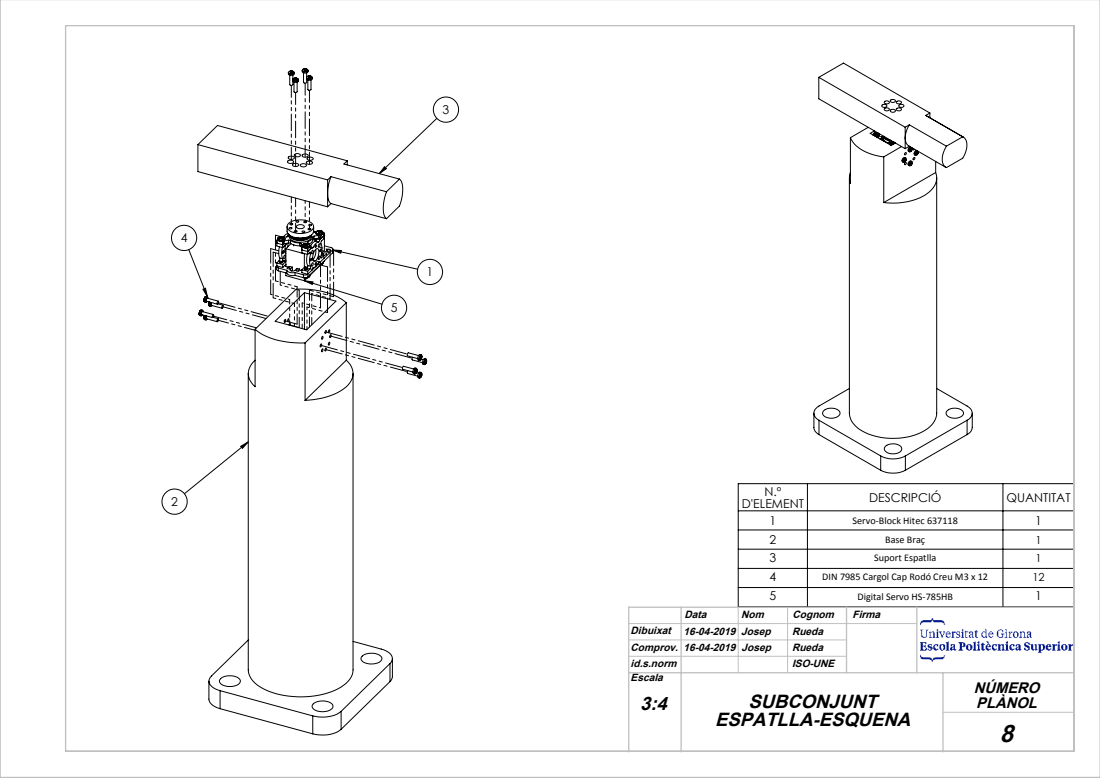
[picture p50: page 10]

N.º D'ELEMENT | DESCRIPCIÓ | QUANTITAT

1 | Servo-Block Hitec 637118 | 1
2 | Base Braç | 1
3 | Suport Espatlla | 1
4 | DIN 7985 Cargol Cap Rodó Creu M3 x 12 | 12
5 | Digital Servo HS-785HB | 1

Data | Nom | Cognom | Firma

Dibuixat | 16-04-2019 | Josep | Rueda
Comprov. | 16-04-2019 Josep | | Rueda
id.s.norm | | | ISO-UNE
Escala 3:4 | SUBCONJUNT ESPATLLA-ESQUENA | NÚMERO PLÀNOL

14

37

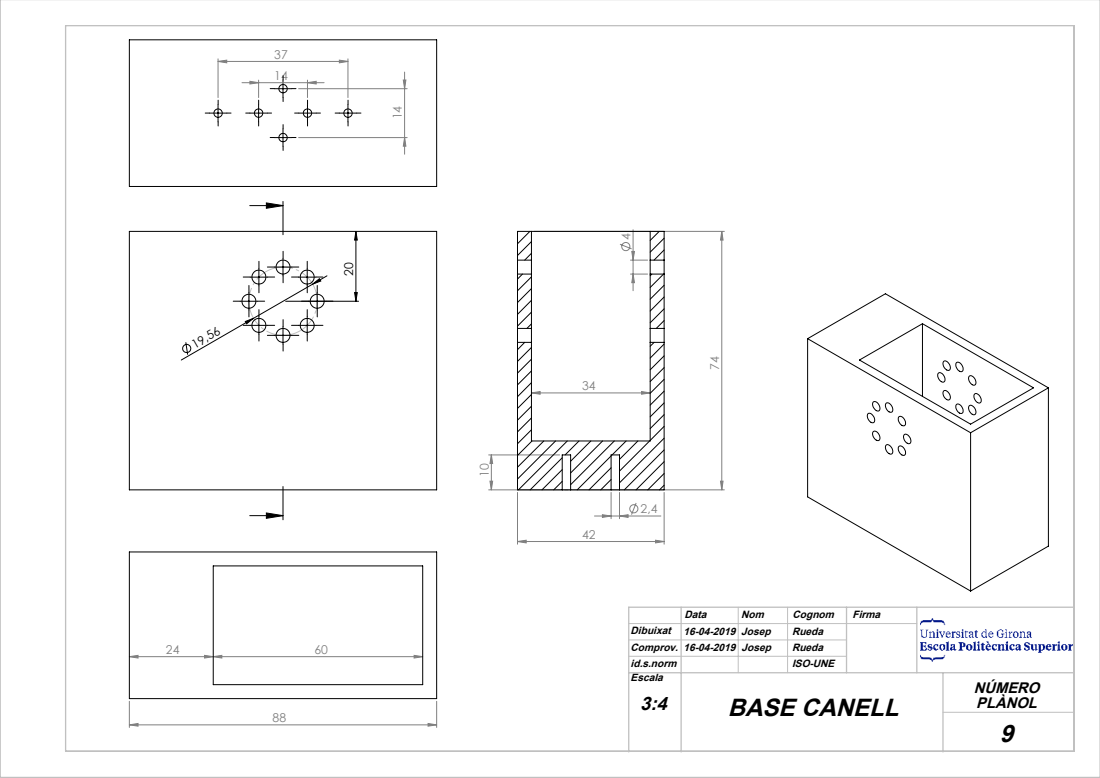
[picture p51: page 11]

Data | Nom | Cognom | Firma
Escala 3:4 | BASE CANELL | NÚMERO PLÀNOL

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

4


N.º D'ELEMENT | DESCRIPCIÓ | QUANTITAT
1 | Suport Canell | 1
2 | Tub perfil rectangular 45 x 20 x 1,2 | 1
3 | Digital Servo HS-785HB | 1
4 | DIN 7981 Auto-roscant Cap Rodó Creu ST2,9 x 6,5 | 16
5 | Prisma 42,6 x 17,6 x 24 | 1

Data | Nom | Cognom | Firma
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

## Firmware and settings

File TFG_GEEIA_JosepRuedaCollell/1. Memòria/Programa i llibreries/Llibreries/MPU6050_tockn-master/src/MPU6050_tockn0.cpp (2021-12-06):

#include "MPU6050_tockn0.h"
#include "Arduino.h"

MPU60500::MPU60500(TwoWire &w){
	wire = &w;
	accCoef = 0.02f;
	gyroCoef = 0.98f;
}

MPU60500::MPU60500(TwoWire &w, float aC, float gC){
	wire = &w;
	accCoef = aC;
	gyroCoef = gC;
}

void MPU60500::begin(){
	writeMPU6050(MPU6050_SMPLRT_DIV, 0x00);
	writeMPU6050(MPU6050_CONFIG, 0x00);
	writeMPU6050(MPU6050_GYRO_CONFIG, 0x08);
	writeMPU6050(MPU6050_ACCEL_CONFIG, 0x00);
	writeMPU6050(MPU6050_PWR_MGMT_1, 0x01);
	this->update();
	angleGyroX = 0;
	angleGyroY = 0;
  angleX = this->getAccAngleX();
  angleY = this->getAccAngleY();
  preInterval = millis();
}

void MPU60500::writeMPU6050(byte reg, byte data){
	wire->beginTransmission(MPU6050_ADDR);
	wire->write(reg);
	wire->write(data);
	wire->endTransmission();
}

byte MPU60500::readMPU6050(byte reg) {
	wire->beginTransmission(MPU6050_ADDR);
	wire->write(reg);
	wire->endTransmission(true);
	wire->requestFrom((uint8_t)MPU6050_ADDR, (size_t)2/*length*/);
	byte data =  wire->read();
	wire->read();
	return data;
}

void MPU60500::setGyroOffsets(float x, float y, float z){
	gyroXoffset = x;
	gyroYoffset = y;
	gyroZoffset = z;
}

void MPU60500::calcGyroOffsets(bool console){
	float x = 0, y = 0, z = 0;
	int16_t rx, ry, rz;

  delay(1000);
	if(console){
    Serial.println();
    Serial.println("========================================");
		Serial.println("calculate gyro offsets");
		Serial.print("DO NOT MOVE A MPU6050");
	}
	for(int i = 0; i < 3000; i++){
		if(console && i % 1000 == 0){
			Serial.print(".");
		}
		wire->beginTransmission(MPU6050_ADDR);
		wire->write(0x3B);
		wire->endTransmission(false);
		wire->requestFrom((int)MPU6050_ADDR, 14, (int)true);

		wire->read() << 8 | wire->read();
		wire->read() << 8 | wire->read();
		wire->read() << 8 | wire->read();
		wire->read() << 8 | wire->read();
		rx = wire->read() << 8 | wire->read();
		ry = wire->read() << 8 | wire->read();
		rz = wire->read() << 8 | wire->read();

		x += ((float)rx) / 65.5;
		y += ((float)ry) / 65.5;
		z += ((float)rz) / 65.5;
	}
	gyroXoffset = x / 3000;
	gyroYoffset = y / 3000;
	gyroZoffset = z / 3000;

	if(console){
    Serial.println();
		Serial.println("Done!!!");
		Serial.print("X : ");Serial.println(gyroXoffset);
		Serial.print("Y : ");Serial.println(gyroYoffset);
		Serial.print("Z : ");Serial.println(gyroZoffset);
		Serial.println("Program will start after 3 seconds");
    Serial.print("========================================");
		delay(3000);
	}
}

void MPU60500::update(){
	wire->beginTransmission(MPU6050_ADDR);
	wire->write(0x3B);
	wire->endTransmission(false);
	wire->requestFrom((int)MPU6050_ADDR, 14, (int)true);

	rawAccX = wire->read() << 8 | wire->read();
	rawAccY = wire->read() << 8 | wire->read();
	rawAccZ = wire->read() << 8 | wire->read();
	rawTemp = wire->read() << 8 | wire->read();
	rawGyroX = wire->read() << 8 | wire->read();
	rawGyroY = wire->read() << 8 | wire->read();
	rawGyroZ = wire->read() << 8 | wire->read();

	temp = (rawTemp + 12412.0) / 340.0;

	accX = ((float)rawAccX) / 16384.0;
	accY = ((float)rawAccY) / 16384.0;
	accZ = ((float)rawAccZ) / 16384.0;

//	angleAccX = atan2(accY, accZ + abs(accX)) * 360 / 2.0 / PI;
//	angleAccY = atan2(accX, accZ + abs(accY)) * 360 / -2.0 / PI;

	angleAccY = atan2(accZ, accX + abs(accY)) * 360 / 2.0 / PI;
	angleAccZ = atan2(accY, accX + abs(accZ)) * 360 / -2.0 / PI;

	gyroX = ((float)rawGyroX) / 65.5;
	gyroY = ((float)rawGyroY) / 65.5;
	gyroZ = ((float)rawGyroZ) / 65.5;

	gyroX -= gyroXoffset;
	gyroY -= gyroYoffset;
	gyroZ -= gyroZoffset;

gyroX = gyroX -0.00;

	interval = (millis() - preInterval) * 0.001;
	intervalX = (millis() - preInterval) * 0.001;

if(gyroX < -0.5 || gyroX > +0.5)
{
	angleGyroX += gyroX * intervalX;
}
else
{
	gyroX=0;
	angleGyroX += gyroX * intervalX;
}

angleGyroY += gyroY * interval;
angleGyroZ += gyroZ * interval;

//	angleX = (gyroCoef * (angleX + gyroX * interval)) + (accCoef * angleAccX);
//	angleY = (gyroCoef * (angleY + gyroY * interval)) + (accCoef * angleAccY);
//	angleZ = angleGyroZ;

	angleY = (gyroCoef * (angleY + gyroY * interval)) + (accCoef * angleAccY);
	angleZ = (gyroCoef * (angleZ + gyroZ * interval)) + (accCoef * angleAccZ);
	angleX = angleGyroX;

	preInterval = millis();

}
